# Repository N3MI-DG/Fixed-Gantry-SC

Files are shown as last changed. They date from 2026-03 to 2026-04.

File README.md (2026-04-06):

# Fixed Gantry StealthChanger Mod

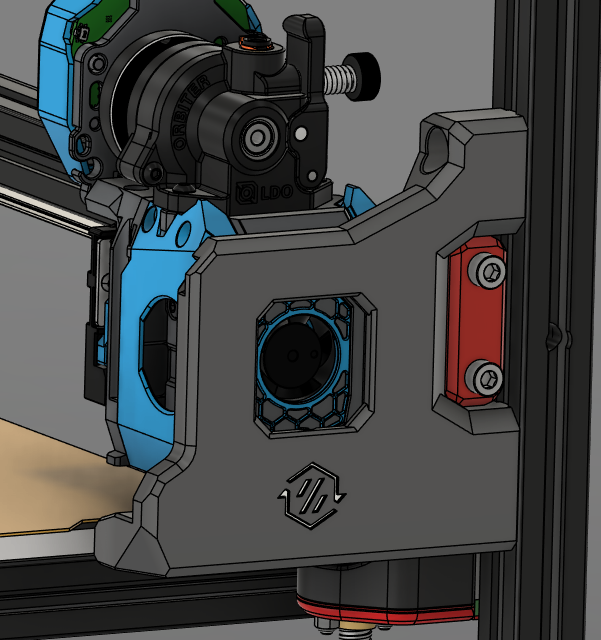
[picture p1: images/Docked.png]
Docked


## Overview

This mod adds StealthChanger capability to fixed gantry printers. It uses a custom dock design that mounts directly to the printer frame and uses a ramping system to mount the toolhead.

The ramping is broken into two actions:

1. The tool runs into the dock in the Y direction, lifting it partially and aligning the screws that are on the tool to the dock.
2. The tool then gets shoved in the X direction to fully lift the tool from the shuttle and engage with the dock.

While a little crude, it works really well and is very reliable.

## Printing

Print with Typical Voron Recommended settings

* `Layer Height` - 0.2mm
* `Extrusion Width` - 0.4mm, forced
* `Infill Percentage` - 40%
* `Infill Type` - Grid, Gyroid, honeycomb, Triangle or Cubic
* `Wall Count` - 4
* `Solid Top/Bottom Layers` - 5
* `Layer Height` - 0.2mm
* `Supports` - Not required, models have built in supports.

## Credits

[DraftShift Design](https://github.com/DraftShift) - StealthChanger

[hartk1213](https://github.com/hartk1213) - Anthead and Umbilical plate aesthetics.

[Armchair-Heavy-Industries](https://github.com/Armchair-Heavy-Industries) - A4T

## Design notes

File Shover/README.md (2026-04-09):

# Shover for Fixed Gantry StealthChanger

## Printing

Print the shover version for the variant of CNC shuttle you have using typical Voron settings.

## BOM

- M3x6 BHCS x2
- M3x8 BHCS x2
- M3x12 BHCS x2
- M3x16 SHCS x1
- M3 Heat Insert x2
- 4mm OD PTFE 12mm Long x2 (optional)

## Instructions

### Step 1

Remove the built-in supports from the shover.

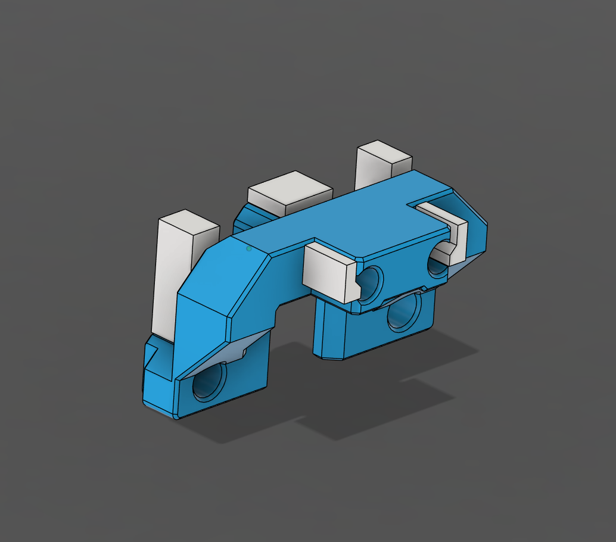
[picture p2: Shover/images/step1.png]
step1


### Step 2

Install 2 M3 heat inserts into the front of the shover.

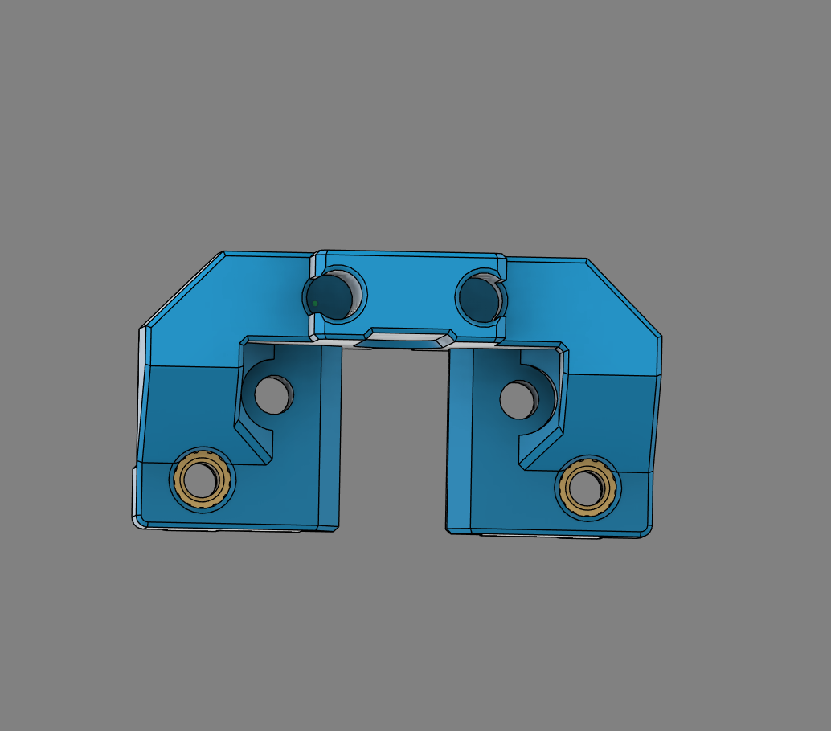
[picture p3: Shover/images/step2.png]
step2


### Step 3

Install a M3x16 SHCS screw into the rear of the shover.

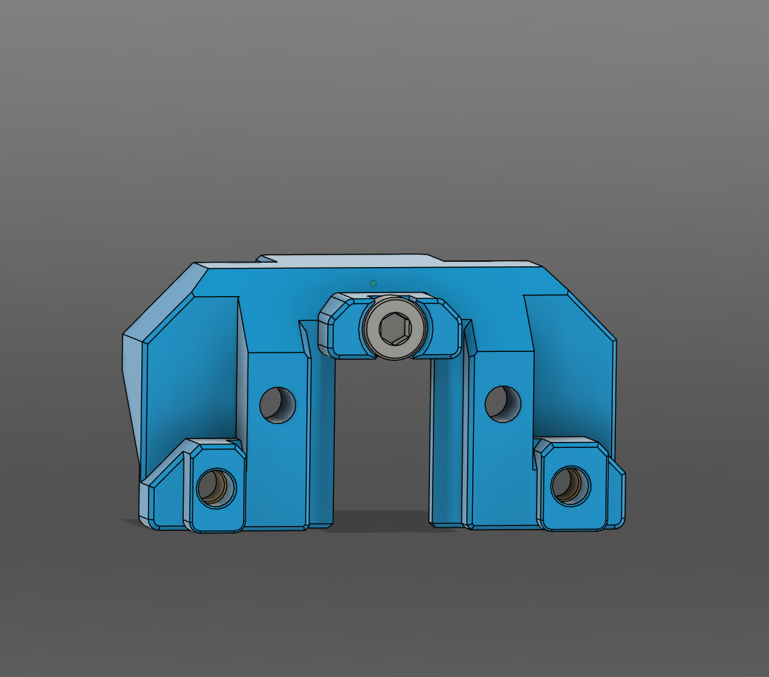
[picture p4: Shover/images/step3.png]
step3


### Step 4

Optionally install 2 12mm pieces of PTFE tube into the front of the shover and trim the corners to match the profile.

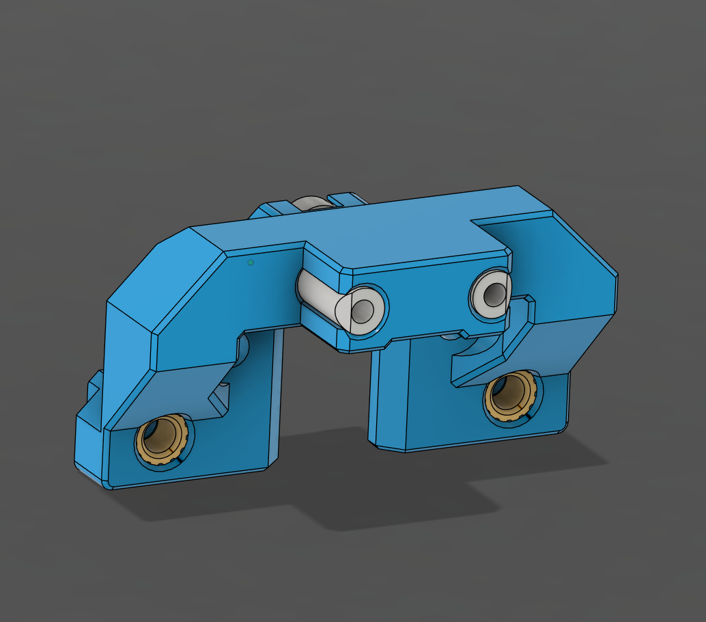
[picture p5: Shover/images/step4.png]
step4


### Step 5

Remove the lower 2 mounting screws from the CNC shuttle and place the shover onto the shuttle. Replace the 2 removed screws with 2 M3x12 BHCS screws.

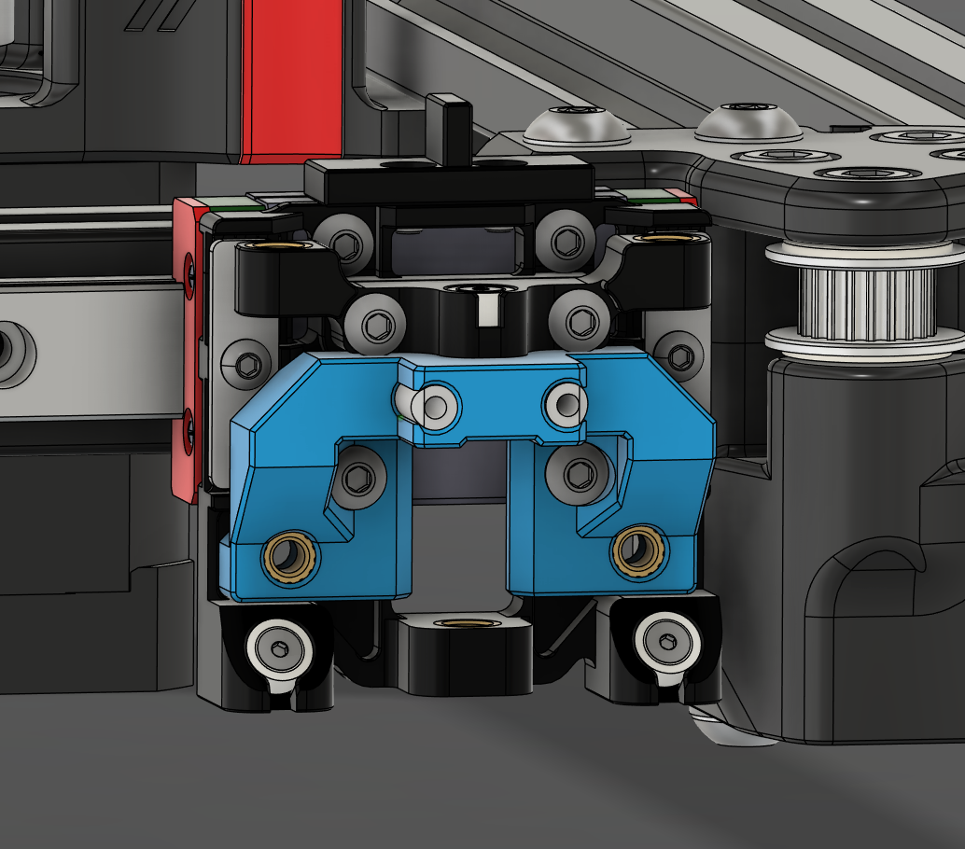
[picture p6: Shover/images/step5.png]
step5


### Step 6

Secure the shover to the CNC shuttle using 2 M3x8 BHCS screws with washers through the heat inserts.

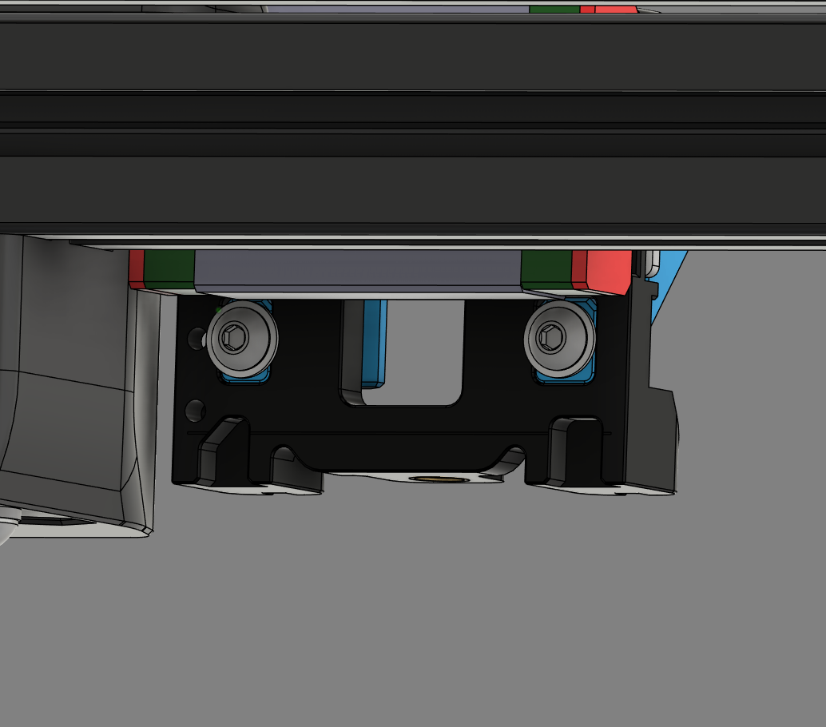
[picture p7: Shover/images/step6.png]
step6


## Testing

After installation, chack that the shover fits neatly in to the backplate of the tool. There should not be any friction between the tool and Shover. If it is too loose without the PTFE, try adding some. If it is too tight with the PTFE, try shaving the PTFE slightly.

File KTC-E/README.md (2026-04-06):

# Klipper-Toolchanger-Easy

To get fixed gantry working on klipper-toolchanger-easy, we need a custom pickup and dropoff path per `tool config` and custom pickup and dropoff gcode in the `[toolchanger]` section.

## Example Tool Sections
The pickup and dropoff paths for the tools need to mirrored. To do that we add a custom path to the `tool config`.

### T0

```
[tool T0]
tool_number: 0
extruder: extruder
fan: T0_part_fan
detection_pin: !nhk0:gpio10
params_park_x: 1.7
params_park_y: 0.8
params_park_z: 1
gcode_x_offset: 0
gcode_y_offset: 0
gcode_z_offset: 0.08
params_dropoff_path: [{'x':22, 'y':16}, {'x':22, 'y':0}, {'x':0, 'y':0}]
params_pickup_path: [{'x':0, 'y':0}, {'x':22, 'y':0}, {'x':22, 'y':16, 'verify':1}]
```

### T1

```
[tool T1]
tool_number: 1
extruder: extruder1
fan: T1_part_fan
detection_pin: !nhk1:gpio10
params_park_x: 302.7
params_park_y: 1.0
params_park_z: 0
gcode_x_offset: -0.290
gcode_y_offset: -1.240
gcode_z_offset: -0.60
params_dropoff_path: [{'x':-22, 'y':16}, {'x':-22, 'y':0}, {'x':0, 'y':0]
params_pickup_path: [{'x':0, 'y':0}, {'x':-22, 'y':0}, {'x':-22, 'y':16, 'verify':1}]
```

## Toolchanger Section
To add custom pickup and dropoff gcodes to the `[toolchanger]` section, add the following to the bottom of the `[toolchanger]` section. This will override the original pickup and dropoff gcodes which are intended for a Voron 2.4.

```
dropoff_gcode:
  {% set x = tool.params_park_x|float %}
  {% set y = tool.params_park_y|float %}
  {% set z = tool.params_park_z|float %}
  {% set fast = tool.params_fast_speed|float %}
  {% set path = tool.params_dropoff_path %}
  {% set max_z = printer.configfile.config["stepper_z"]["position_max"]|float %}
  {% set cur_z = printer.toolhead.position[2]|float %}
  RESPOND TYPE=echo MSG='Dropping off {tool.name}'
  G90
  ; Move 1 mm up to avoid crashing into things
  G0 Z{ [cur_z+1.0, max_z]|min } F{fast}
  #   ##############  Move up to the dock  ##############
  ROUNDED_G0 X={x + path[0]['x']|float} D=150 F={fast}
  ROUNDED_G0 Y={y + path[0]['y']|float} D=0 F={fast}
  STOP_CRASH_DETECTION
  #  ############## Run the path ##############
  {% for pos in path %}
    {% set speed = tool.params_path_speed|float * (pos.get('f', 1.0)|float) %}
    G0 {% if 'x' in pos %}X{x + pos['x']|float}{% endif %} {% if 'y' in pos %}Y{y + pos['y']|float}{% endif %} {% if 'z' in pos %}Z{z + pos['z']|float }{% endif %} F{speed}
  {% endfor %}
  ## Return to safe Y if no pickup_tool
  {% if pickup_tool is none %}
    G0 Y{tool.params_safe_y} F{fast}
  {% endif %}

pickup_gcode:
  {% set x = tool.params_park_x|float %}
  {% set y = tool.params_park_y|float %}
  {% set z = tool.params_park_z|float %}
  {% set fast = tool.params_fast_speed|float %}
  {% set path = tool.params_pickup_path %}
  RESPOND TYPE=echo MSG='Picking up {tool.name}'
  G90
  #   ##############  Fast to the last point  ##############
  ROUNDED_G0 Y={tool.params_close_y} F={fast} D=5
  # ROUNDED_G0 X={x} Z={z + path[0]['z']|float} F={fast} D=5
  ROUNDED_G0 X={x} F={fast} D=5
  ROUNDED_G0 Y={y + path[0]['y']|float} F={fast} D=0
  # Wait for temp before actually picking up the tool, while the nozzle is resting on it's pad.
  {% if tool.extruder %}
    M109 T{tool.tool_number} S{printer[tool.extruder].target|int}
  {% endif %}
  # Run the path
  {% for pos in path %}
    {% set speed = tool.params_path_speed|float * (pos.get('f', 1.0)|float) %}
    G0 {% if 'x' in pos %}X{x + pos['x']|float}{% endif %} {% if 'y' in pos %}Y{y + pos['y']|float}{% endif %} {% if 'z' in pos %}Z{z + pos['z']|float }{% endif %} F{speed}
    {% if 'verify' in pos %}
      VERIFY_TOOL_DETECTED T={tool.tool_number}
    {% endif %}
  {% endfor %}
  # Restore the position with smooth rounded move.
  ROUNDED_G0 Y={tool.params_safe_y} F={fast} D=20
  ROUNDED_G0 D=0
```

## Z Tilt

The Z tilt positions will need to be adjusted because of the tool's docked position. This is an example of what I am using on my 300 Trident.

```
[z_tilt]
z_positions:
  -50, 18
  150, 348
  350, 18
points:
  20, 25
  152.5, 250
  285, 25
```

### Macro to remove tool during Z tilt (Cartographer Only)

```
[gcode_macro Z_TILT_ADJUST]
rename_existing: ZZ_TILT_ADJUST
gcode:
  {% if printer.toolchanger.tool_number != -1 %}
    UNSELECT_TOOL
  {% endif %}

  ZZ_TILT_ADJUST
  ```

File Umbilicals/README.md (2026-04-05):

# Umbilicals for Fixed Gantry StealthChanger (Trident)

## Printing

### TPU

- Clip x2 Minimum (More clips or cable ties can be used to hold the cable and PTFE together over the length of the umbilical.)
- Terminator x1
- Terminator (Mirrored) x1

### ABS/ASA

- Face Plate x1
- Outer Plate x1
- Cover Left x1
- Cover Right x1
- LED Diffuser x1 (Optional)

## BOM

- M3x6 BHCS x2
- M3x10 SHCS x4
- M5x10 BHCS x2
- M3 Heat Insert x8
- M5 Roll-in T Nut x2
- 3x0.3mm Flat Spring Steel x2

## Instructions

### Step 1

Install 6 M3 heat inserts in to the Face Plate.

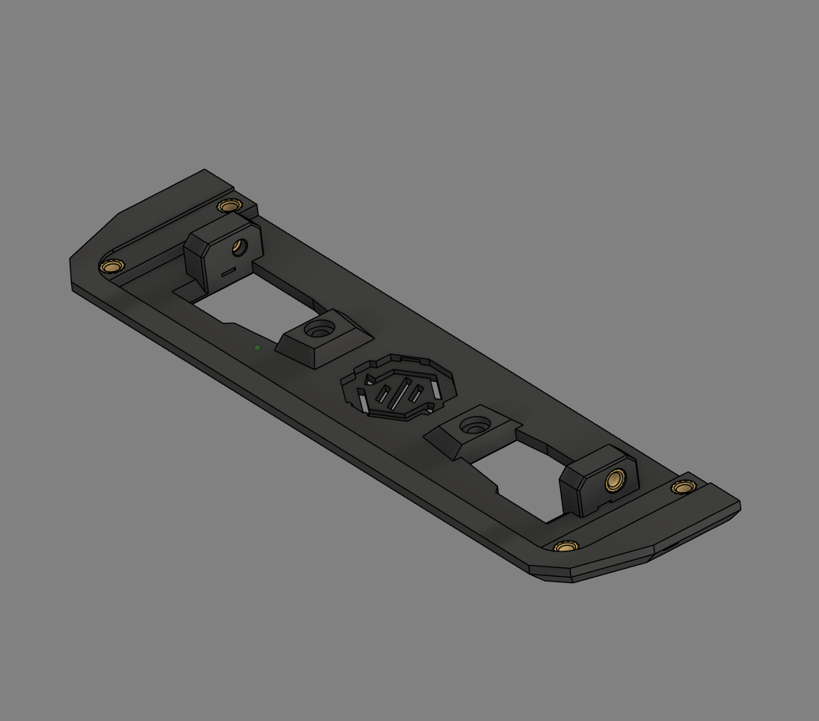
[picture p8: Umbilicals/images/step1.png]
step1


### Step 2

Install a heat insert in to each of the covers.

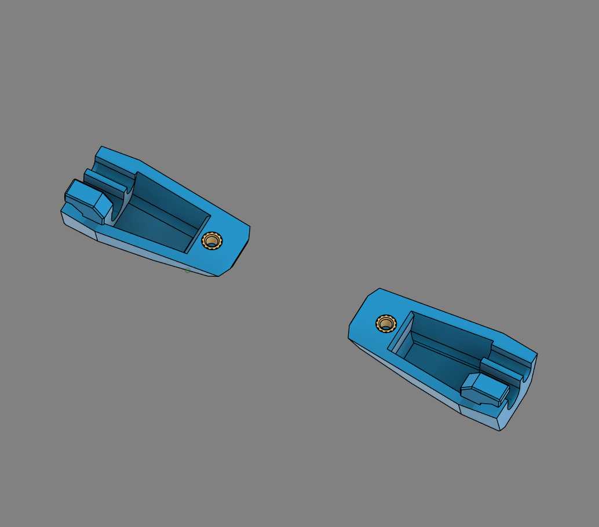
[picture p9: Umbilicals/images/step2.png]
step2


### Step 3 (Optional)

Install the diffuser in to the Face Plate.

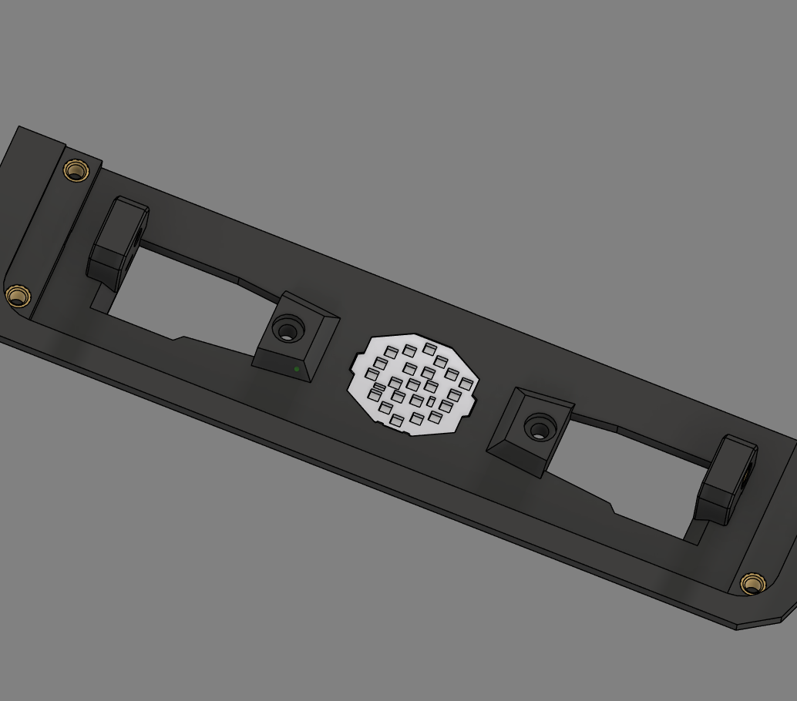
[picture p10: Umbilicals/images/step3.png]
step3


### Step 4 (Optional)

Apply 1mm foam around the perimiter of the Face Plate.

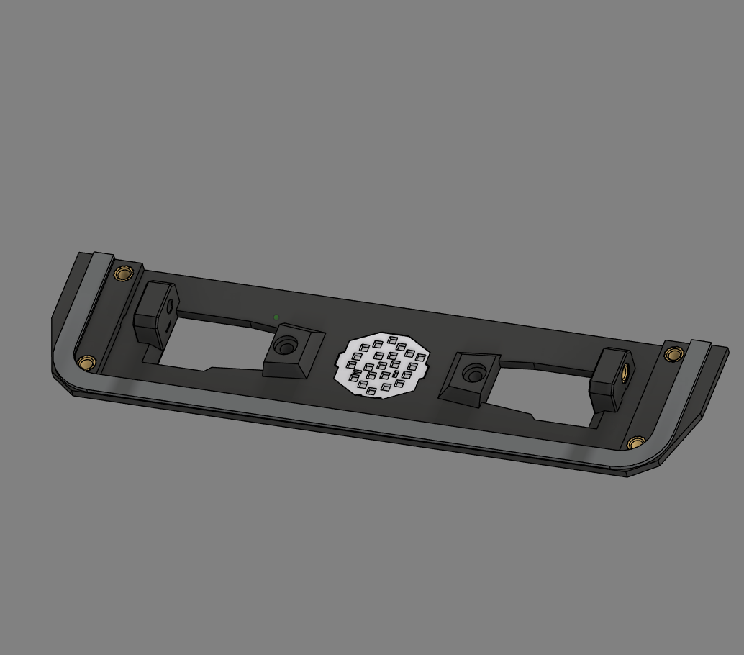
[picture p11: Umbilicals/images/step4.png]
step4


### Step 5

Bend a piece of 3x0.3mm spring steel 90 degrees and feed it through the faceplate. To get the correct length, the spring steel should reach the inside of the printers frame when the faceplate is in place.

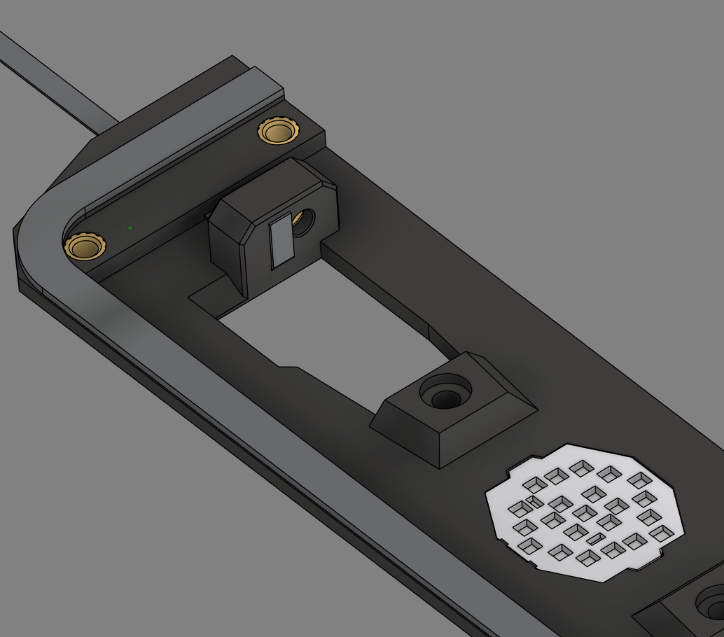
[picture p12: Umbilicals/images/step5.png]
step5


### Step 6

Secure both pieces of spring steel with a m3x6mm BHCS screw.

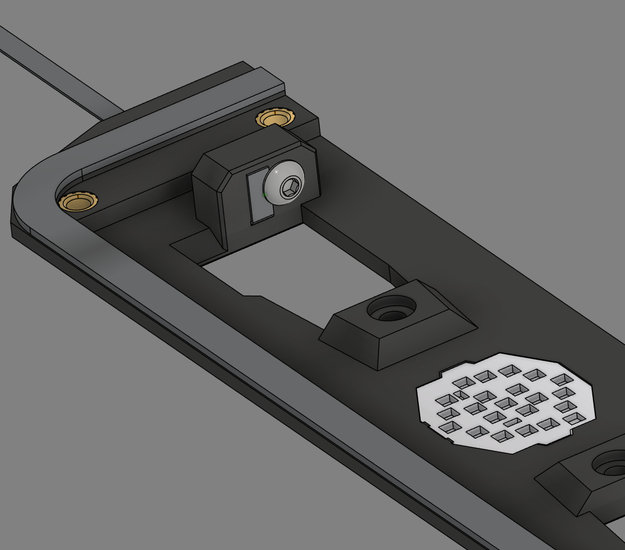
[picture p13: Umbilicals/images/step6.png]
step6


### Step 7

Install a TPU Clip and Terminatior ensuring the orientation is correct. The cable should be on the bottom and PTFE on top.

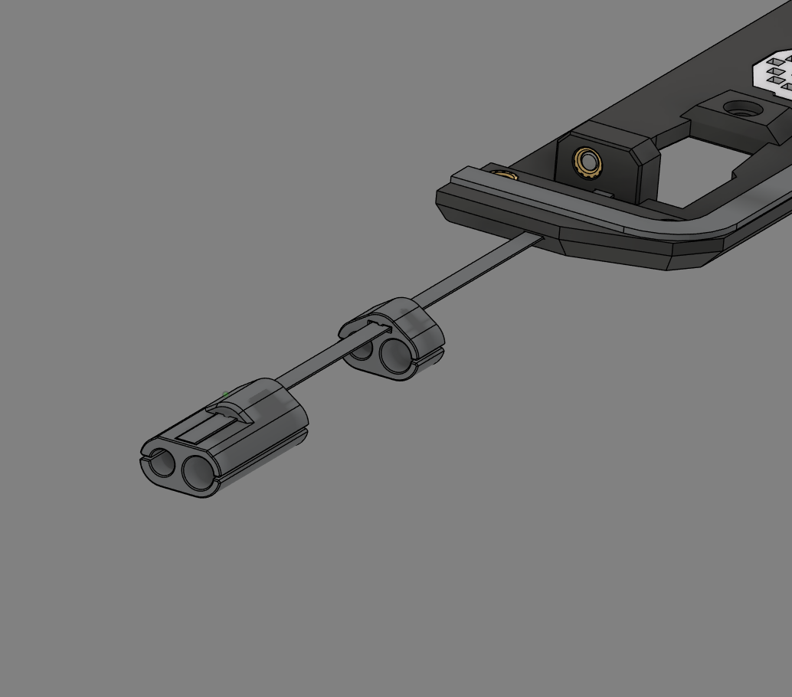
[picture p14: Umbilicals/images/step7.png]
step7


### Step 8

Put a small bend in the end of the spring steel to keep the TPU Terminator in place.

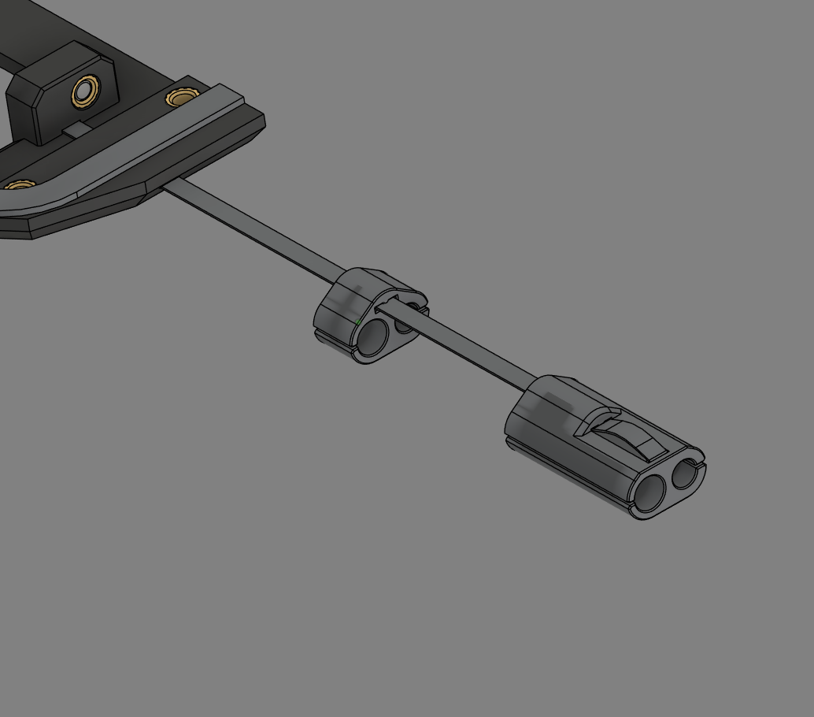
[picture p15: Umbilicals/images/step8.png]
step8


### Step 9

Attach the Outer Plate to the printer using 2 M5x10 BHCS screws and 2 M5 roll-in T nuts.

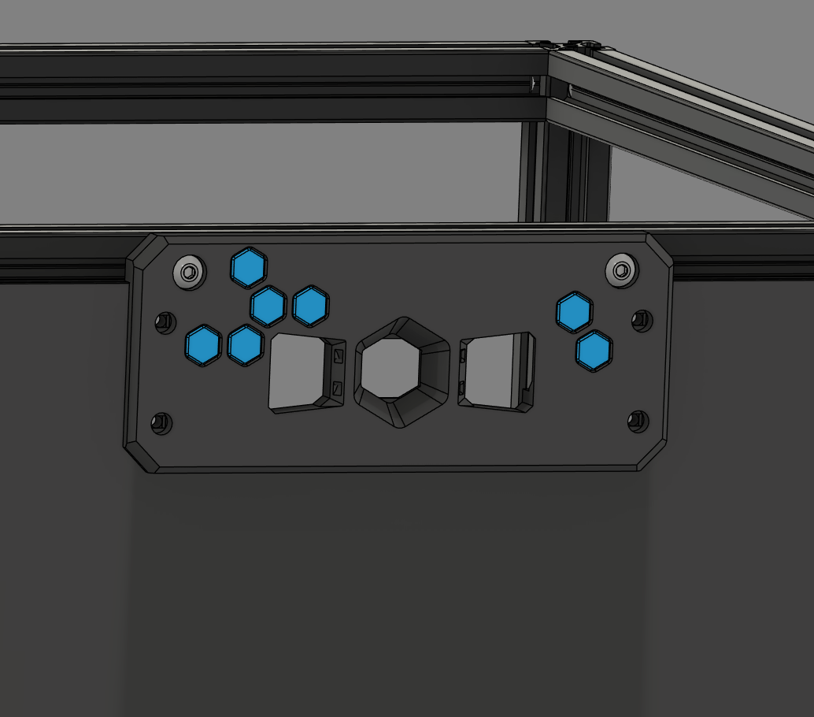
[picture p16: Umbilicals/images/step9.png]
step9


### Step 10 ( Optional)

Install a SC Barf LED.

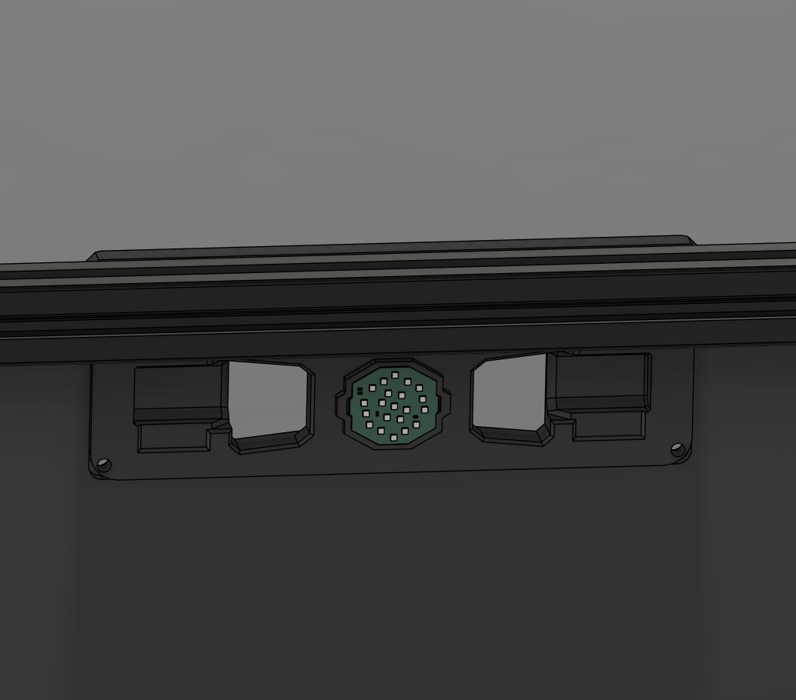
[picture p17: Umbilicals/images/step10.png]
step10


### Step 11

Attach the Face Plate to the Outer Plate using 4 M3x10 BHCS screws.

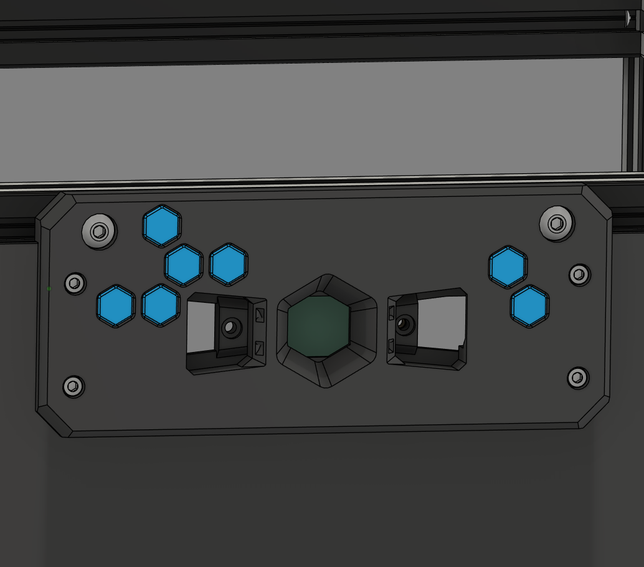
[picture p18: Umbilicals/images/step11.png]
step11


### Step 12

Feed the cables and PTFE tubes through and attach them to the toolheads. Once an umbilical length is determined place the cables and PTFE tubes in to their respective TPU Clip and Terminatior.

### Step 13

Slot the Covers in place and secure with a M3x8 BHCS screw.

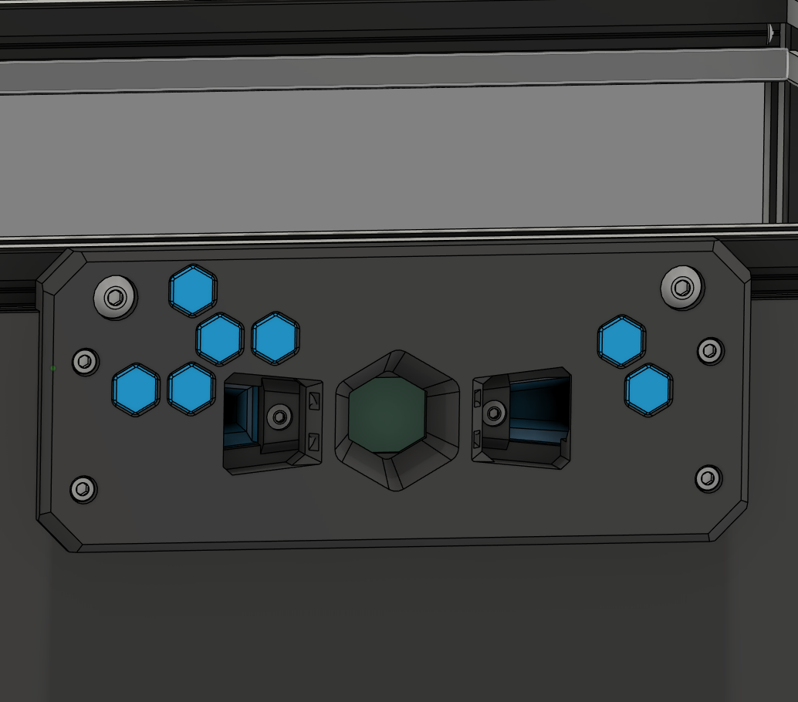
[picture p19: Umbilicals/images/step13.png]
step13


### Step 14

Secure umbilical at the rear of the printer with a ziptie.

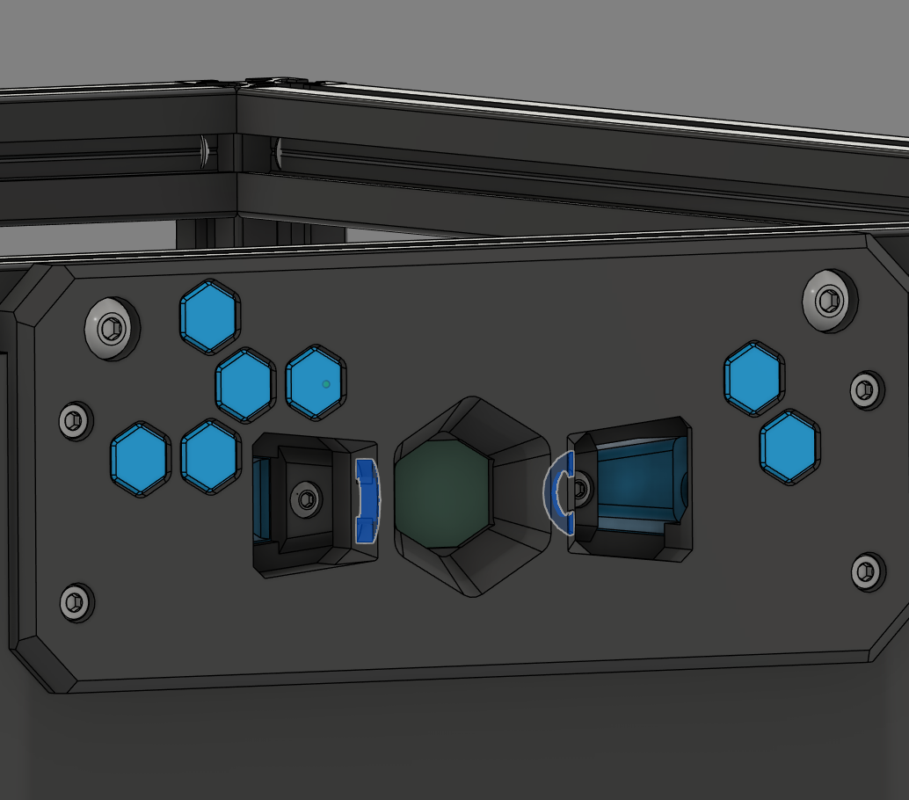
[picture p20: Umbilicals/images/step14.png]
step14


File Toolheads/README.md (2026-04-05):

# Toolheads for Fixed Gantry StealthChanger

The Anthead and A4T are currently supported. Others may be added in the future.

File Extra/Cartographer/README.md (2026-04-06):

# Cartographer Mount

## Printing

- CNC Cartographer Mount x1
- CNC Cartographer Arm x1

## BOM

- M3x20 SHCS x1
- M3x16 SHCS x1
- M3x12 SHCS x1
- M3 Heat Insert x3

## Instructions

### Step 1

Remove built-in supports from the Cartographer Mount.

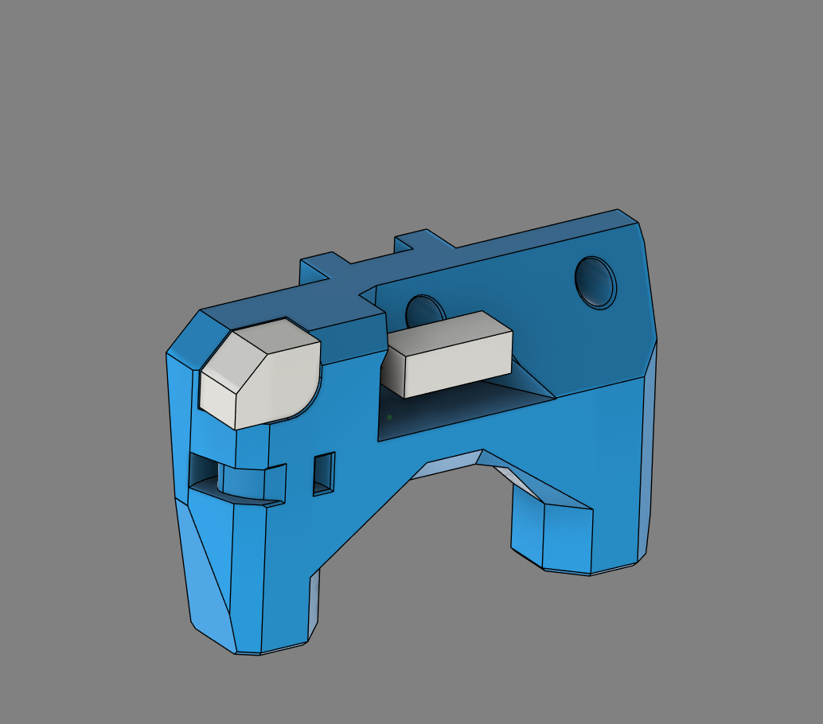
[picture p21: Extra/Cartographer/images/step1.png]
step1


### Step 2

Install 2 heat inserts in to the bottom of the Cartographer Mount.

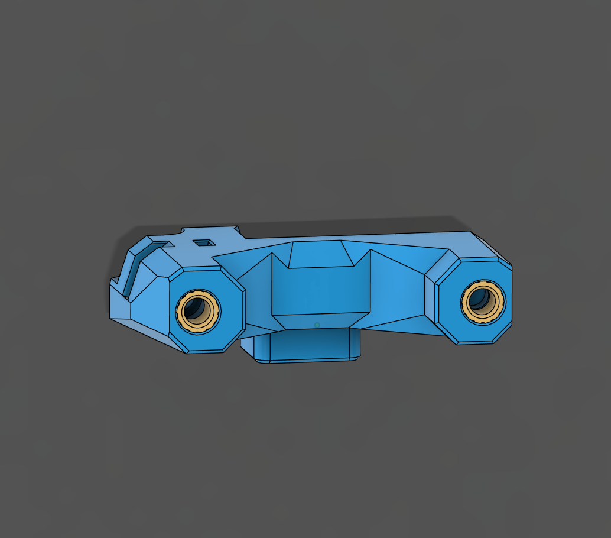
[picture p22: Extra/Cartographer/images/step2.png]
step2


### Step 3

Install a heat insert in to the Cartographer Arm.

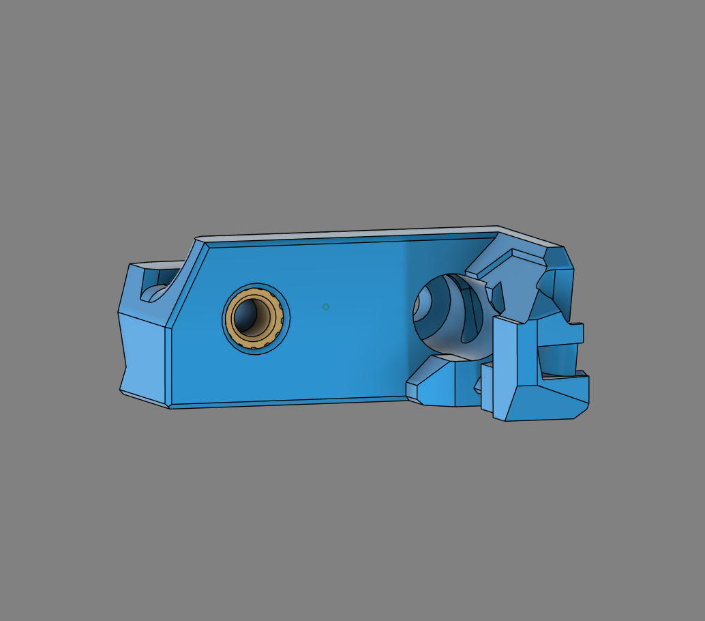
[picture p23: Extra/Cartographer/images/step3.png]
step3


### Step 4

Attach the Cartographer Arm to the Mount with a M3x20 SHCS screw.

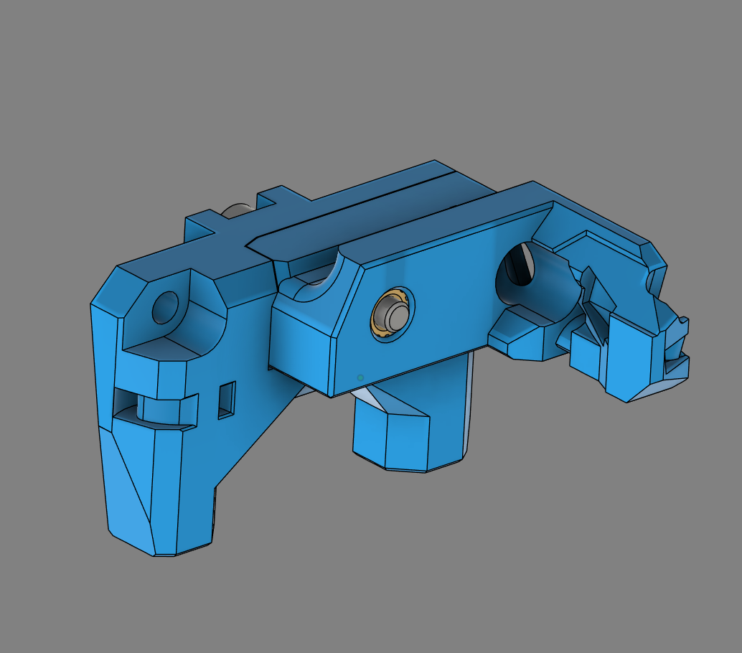
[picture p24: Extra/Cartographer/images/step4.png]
step4


### Step 5

Attach the Cartographer to the mount using the supplied flat screws.

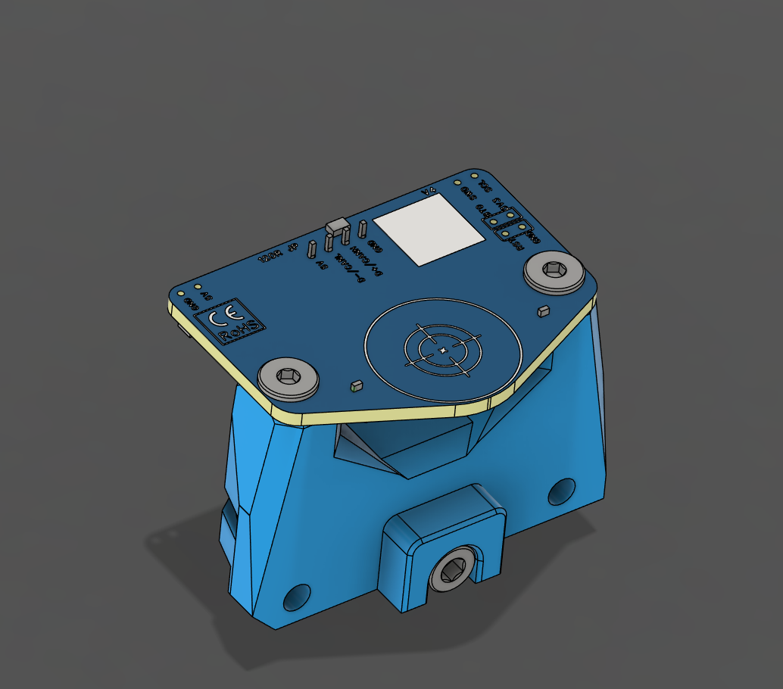
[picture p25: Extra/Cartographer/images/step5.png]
step5


### Step 6

Route the cable through the provided channels and secure using 3 cable ties.

step6

### Step 7

Attach the Cartographer Mount to the Shover On the CNC Shuttle using a M3x12 SHCS screw and a M3x16 SHCS screw.

step7

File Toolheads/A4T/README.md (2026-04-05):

# A4T

All of the A4T cowl variants have been provided, but depending on the cowl variant, some may not be suitable.

The Dragon/Rapido UHF variant in particular has the hotend fan significantly blocked by the dock.

## Printing

- Cowl for your specific hotend.
- Low Rider StealthChanger backplate.

## BOM (Per Toolhead)

- M3x12 BHCS x2

## Instructions

The A4T for this mod requires a custom Cowl and StealthChanger Backplate. The complete toolhead will need to be built.

### Step 1

Assemble the A4T As you would typically, substituting the Cowl and StealthChanger Backplate for the version from this repository.

step1

### Step 2

Install 2 M3x12 BHCS screws in to the front of the cowl. Screw them in until the screw head is ~3mm away from the front of the duct. These will need to be tuned later.

step2

### Step 3

Install a 6x3mm magnet in the bottom of either the left or right side of the StealthChanger Backplate. These magnets can be held in place with either glue or an M2x8 FHCS screw and are only required for the side of the printer the tool will rest in.

NOTE: The magnet needs to attract to the top magnet in the dock's blocker. Make sure it is orientated correctly. 

step3

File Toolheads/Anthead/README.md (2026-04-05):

# Anthead

SF version only.

## Printing

- Left duct
- Right duct

## BOM (Per Toolhead)

- M3x12 BHCS x2

## Instructions

The Anthead for this mod is much the same as the Anthead for a typical StealthChanger. The only difference being modified ducts.

### Step 1

Replace the stock Fan Ducts with the version supplied in this repository.

step1

### Step 2

Install an M3x12 BHCS screw to each of the Fan Ducts. Screw them in until the screw head is ~3mm away from the front of the duct. These will need to be tuned later.

step2

### Step 3

Install a 6x3mm magnet in the bottom of either the left or right side of the duct. These magnets should be held in place with glue and are only required for the side of the printer the tool will rest in.

NOTE: The magnet needs to attract to the top magnet in the dock's blocker. Make sure it is orientated correctly. 

step3

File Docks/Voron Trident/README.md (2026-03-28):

# Voron Trident Docks for StealthChanger

## Printing
For each dock, you will need to print:

- Dock body for your idler configuration.
- Blocker for the chosen toolhead.
- LED diffuser.

## BOM (Per Dock)

All required hardware for the docks can be obtained from the LDO tool and dock kit. 
There are provisions for countersunk 6x3 magnets for the blockers and docks if you have them available.

- M3x6 BHCS x3
- M3x40 SHCS x1
- M5x10 BHCS x2
- M5 Roll-in T Nut x2
- M3 Heat Insert x2
- StealthChanger Wiper x1
- 6x3 Magnet (N52) x4
- 5x2 Magnet (N52) x2
- SC Barf LED x1 (optional)
- M3x6 BHCS x1 (optional)

## Instructions

### Step 1

Install 2 M3 heat inserts in to the bottom of the Blocker.

step1

### Step 2

Install a 6x3mm magnet in to the bottom of the blocker. Use either glue or a M2x8 FHCS screw to secure it depending on the magnet type.

step2

### Step 3

Install a 6x3mm magnet in to the top of the blocker. Use either glue or a M2x8 FHCS screw to secure it depending on the magnet type.

NOTE: The top magnet needs to attract to the bottom of the toolhead. Ensure you install the magnet in the correct orientation.

step3

### Step 4

Insert the wiper in to the blocker and secure with 2 M3x6 BHCS screws. These screws can be loosened to adjust the wiper position later.

step4

### Step 5

Install the wiper tension screw in the bottom of the blocker by screwing it in to the plastic. It doesn't need to be tightened, it is used later to adjust the pressure applied to the nozzle.

step5

### Step 6

Install a 6x3mm magnet in to the bottom of the dock. Use either glue or a M2x8 FHCS screw to secure it depending on the magnet type.

NOTE: The magnet needs to attract to the bottom of the blocker. Ensure you install the magnet in the correct orientation.

step6

### Step 7

Install 2 5x2mm magnets in to the screw slots of the dock. Use glue to secure them.

step7

### Step 8

Install the LED diffuser by pushing the bottom in first and then pushing the top in to place. If you are not using an LED, you can add some glue to help keep it in place.

step8

### Step 9 (Optional)

Place the SC Barf LED in place and secure with an M3x6 BHCS screw.

step9

### Step 10

Install the blocker with an M3x40 SHCS screw. Do not over tighten, the blocker needs to be able to rotate freely on the screw.

step10

### Step 11 

Mount the dock on the printer using 2 M5x10 BHCS screws and 2 M5 roll-in T-nuts. The dock fits over the gantry's idler.

step11

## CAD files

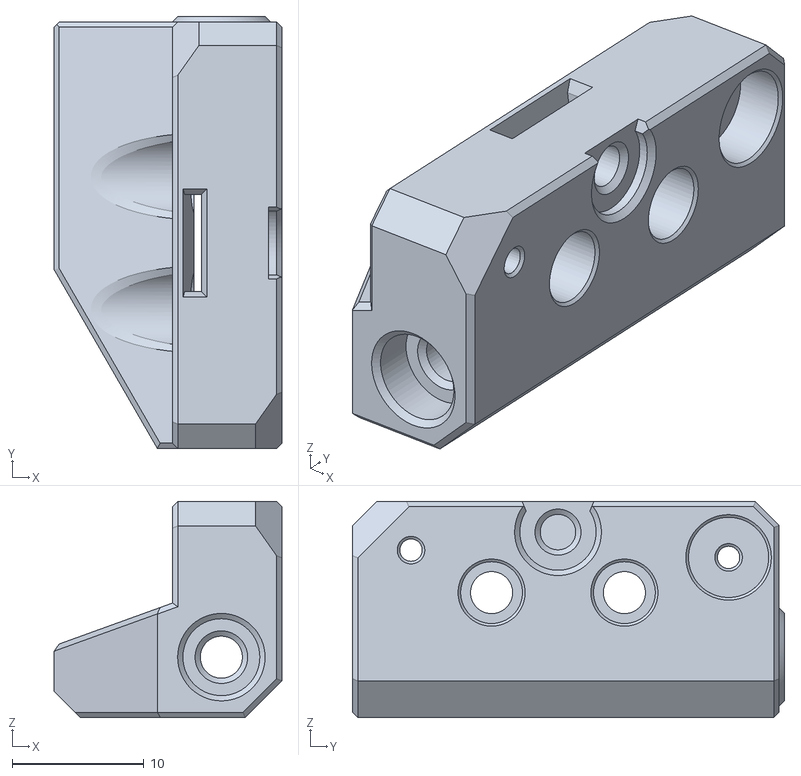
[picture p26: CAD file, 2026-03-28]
Docks/Voron Trident/STLS/Anthead Blocker (Right).stl
17.3 x 32.9 x 16.4

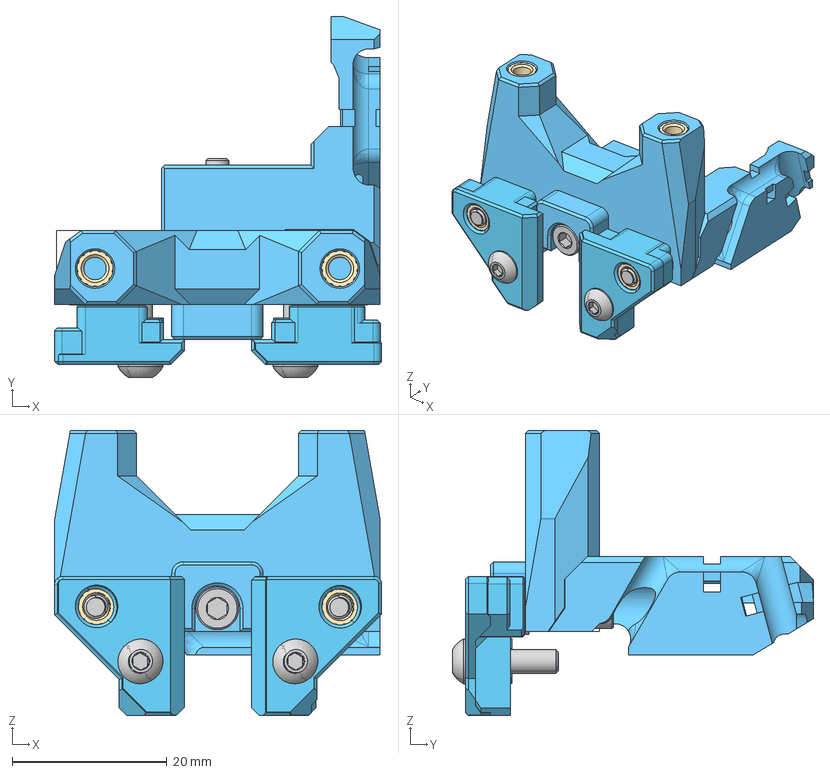
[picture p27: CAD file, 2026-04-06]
Extra/Cartographer/STEP/Carto Mount.step
42.2 x 46.6 x 36.9 mm
CNC Cartographer X Bracket
Supports (8)
M3x12 SHCS
M3x16 SHCS
M3x20 SHCS
(Unsaved) x 3
M3x8 BHCS x 2
(Unsaved)_1 x 2
M3 Shim Washer x 2
M3x12 BHCS x 2
M3x8 BHCS_1 x 2
(Unsaved)_2 x 2
M3 Shim Washer_1 x 2
M3x12 BHCS_1 x 2

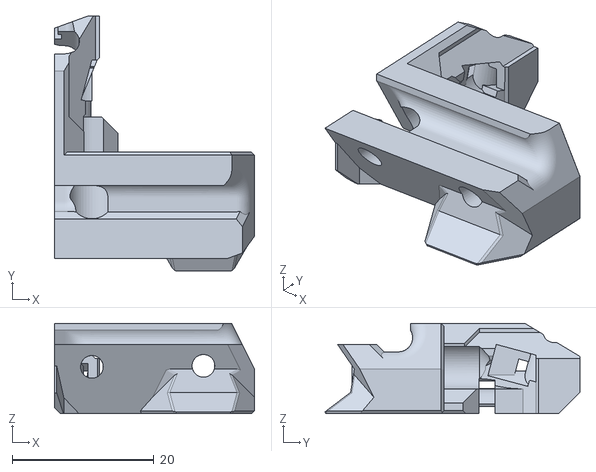
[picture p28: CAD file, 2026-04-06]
Extra/Cartographer/STL/CNC Cartographer Arm.stl
28.2 x 36.0 x 12.7

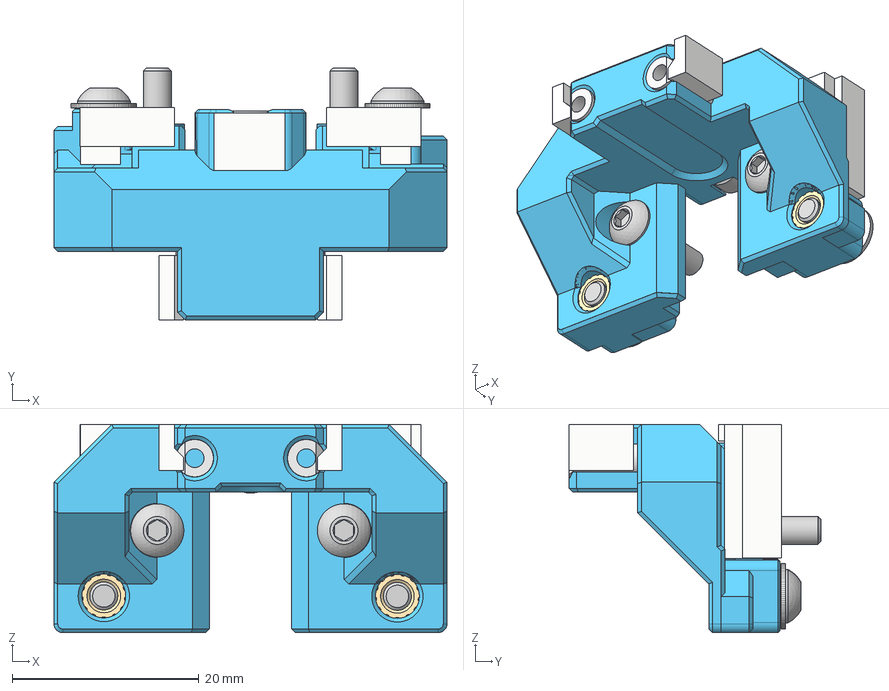
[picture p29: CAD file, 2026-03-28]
Shover/STEP/Shover.step
42.1 x 26.9 x 22.3 mm
M3x8 BHCS x 2
(Unsaved) x 2
M3x16 SHCS
M3 Shim Washer x 2
M3x12 BHCS x 2
PTFE (1)
Supports (7)
M3x8 BHCS_1 x 2
(Unsaved)_1 x 2
M3 Shim Washer_1 x 2
M3x12 BHCS_1 x 2
M3x16 SHCS_1
PTFE
Supports (6)

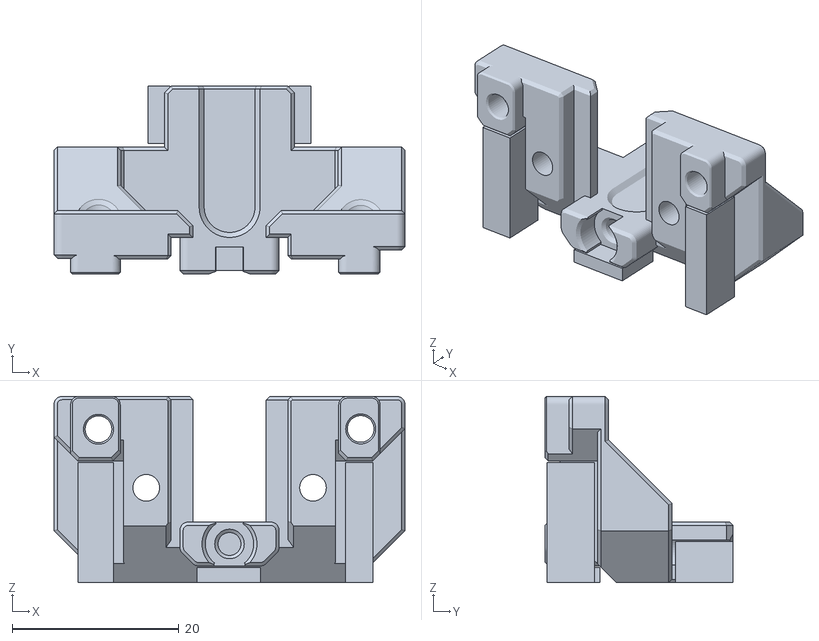
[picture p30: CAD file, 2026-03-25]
Shover/STLS/LDO Shover.stl
42.1 x 22.6 x 22.3

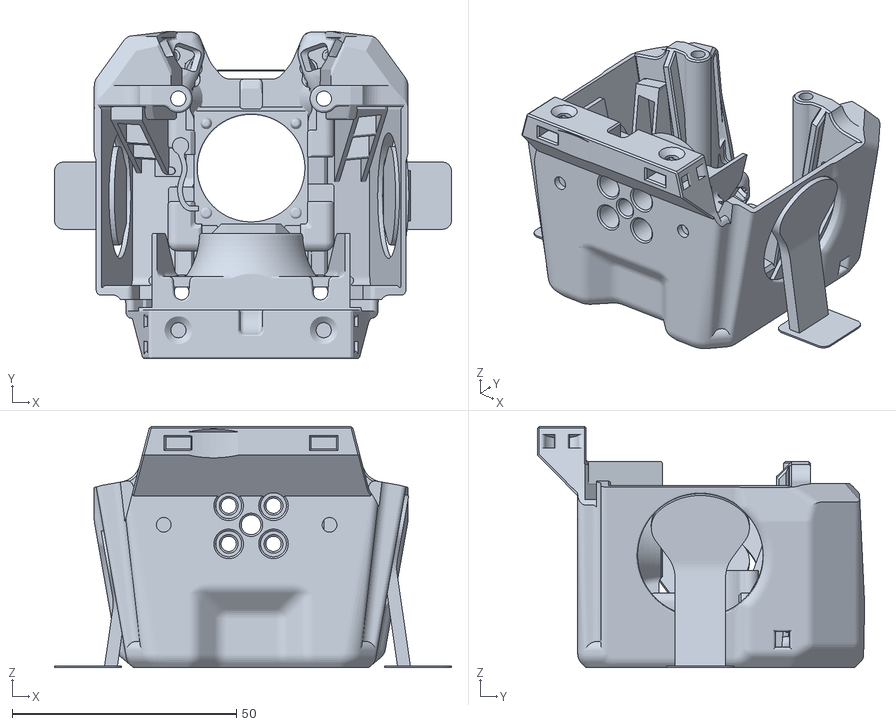
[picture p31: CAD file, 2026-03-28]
Toolheads/A4T/STLS/A4T Cowling - Revo-Voron Orbiter.stl
88.6 x 73.0 x 53.8

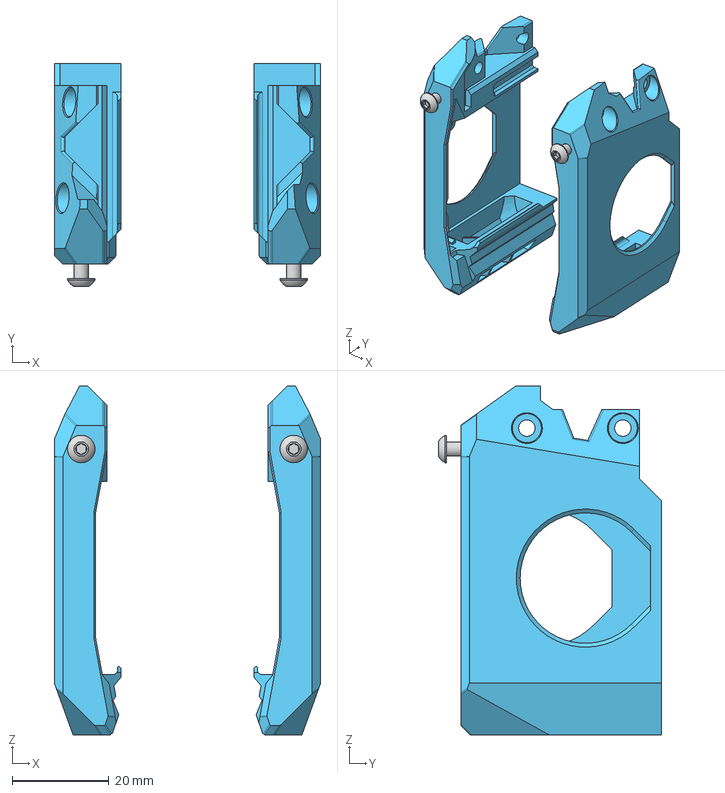
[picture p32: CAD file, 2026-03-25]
Toolheads/Anthead/STEP/Anthead SF Ducts.step
55.2 x 46.3 x 72.3 mm
Right_Duct_Standard
M3x25 BHCS x 2
Left_Duct_Standard

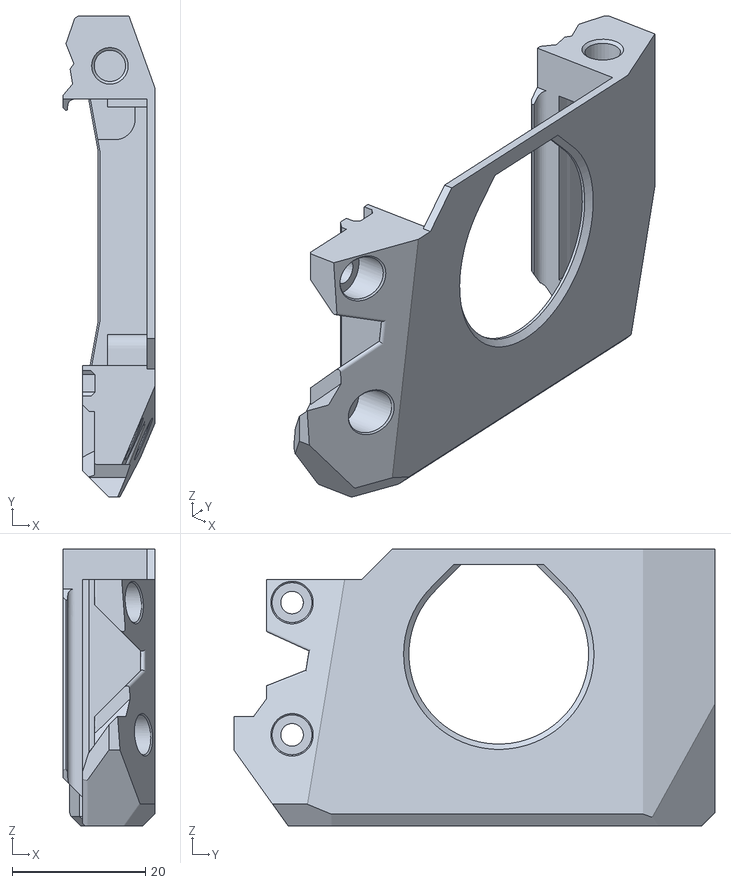
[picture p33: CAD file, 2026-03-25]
Toolheads/Anthead/STLS/Right_Duct_Standard.stl
13.8 x 72.3 x 41.6

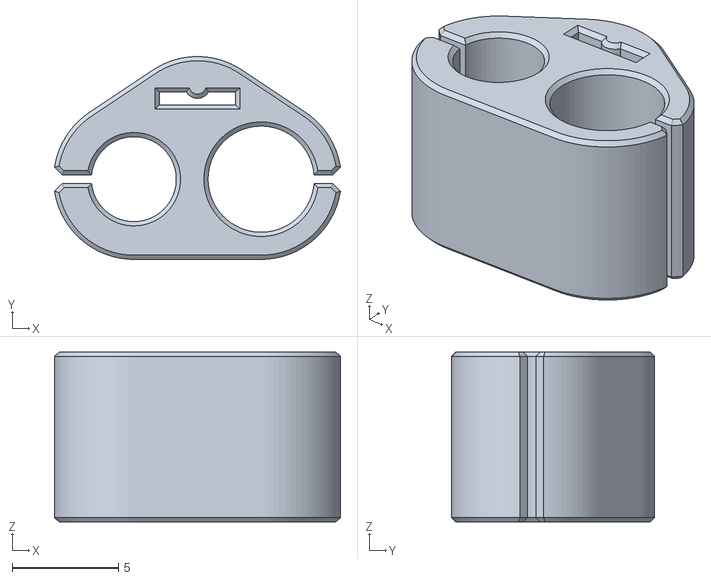
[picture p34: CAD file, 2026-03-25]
Umbilicals/STL/[tpu]_Clip_x2.stl
13.5 x 9.56 x 8.00

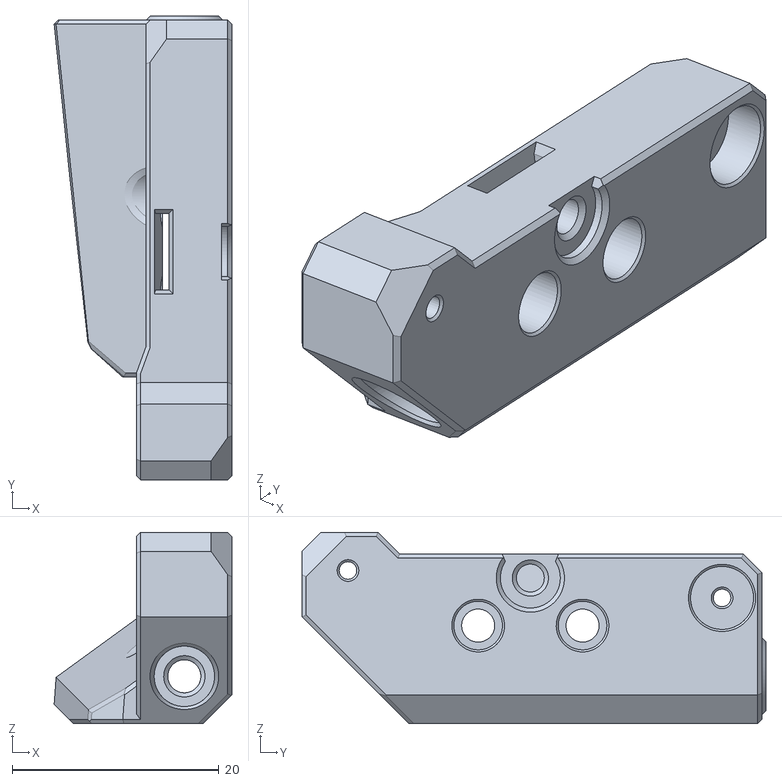
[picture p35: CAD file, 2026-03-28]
Docks/Voron Trident/STLS/A4T Blocker (Right).stl
17.2 x 44.9 x 18.5

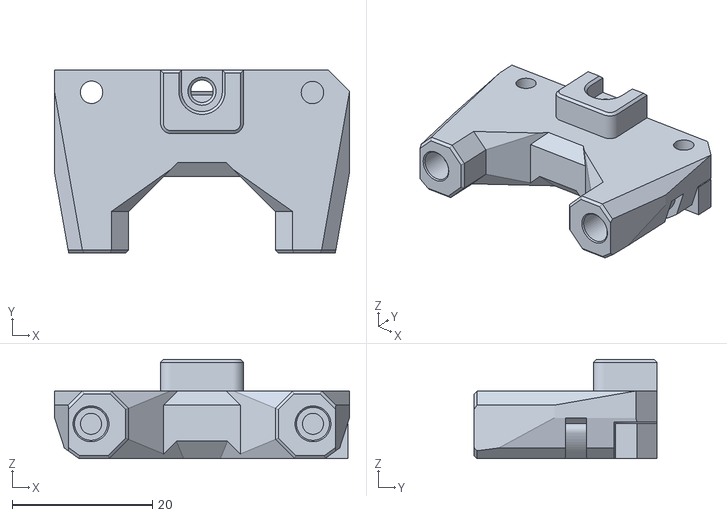
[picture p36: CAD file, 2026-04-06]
Extra/Cartographer/STL/CNC Cartographer Mount.stl
42.0 x 26.0 x 14.1

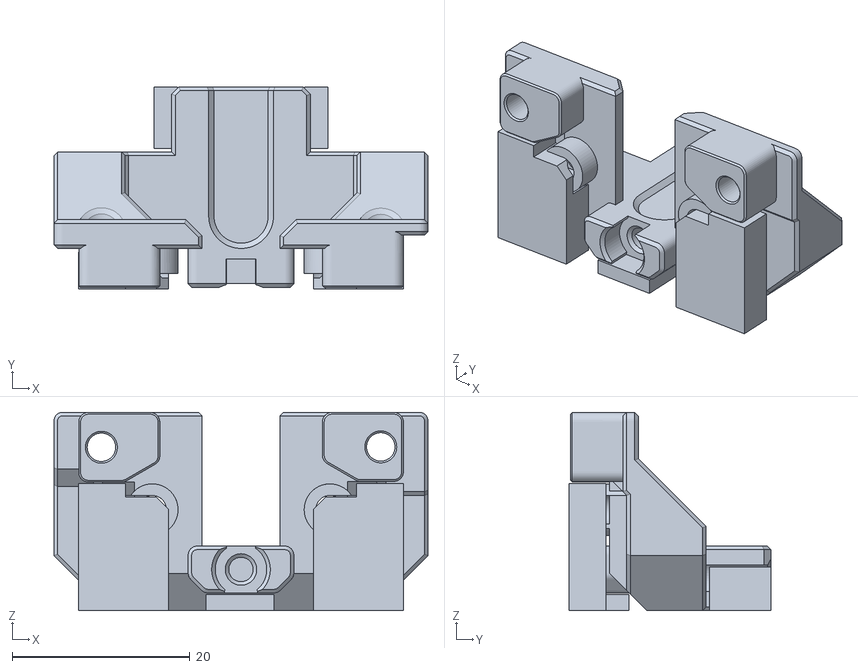
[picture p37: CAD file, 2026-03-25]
Shover/STLS/Fysetc Shover.stl
42.1 x 22.7 x 22.3

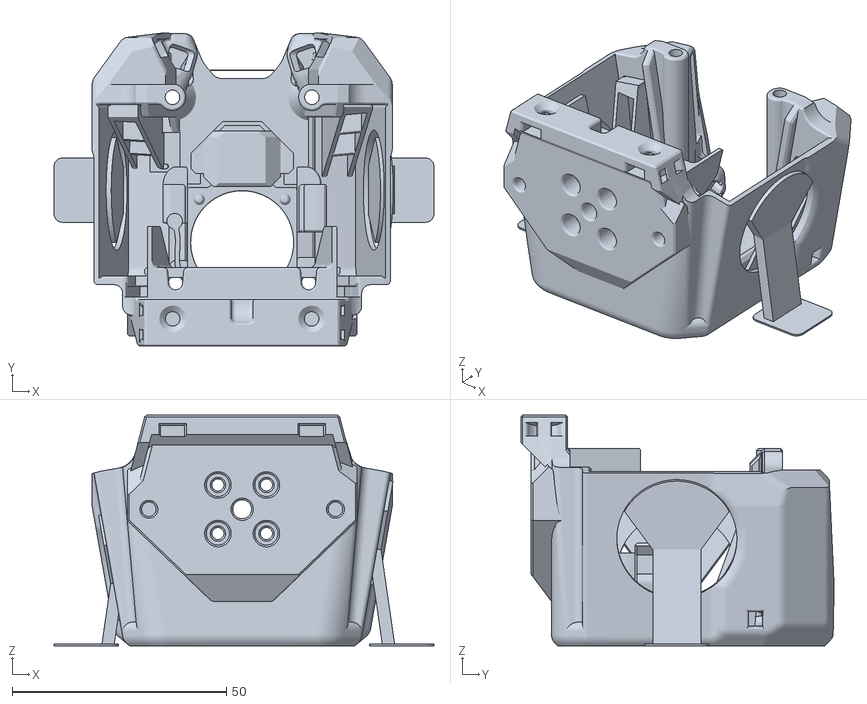
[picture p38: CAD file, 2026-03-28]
Toolheads/A4T/STLS/A4T Cowling - Dragon-Rapido UHF Sherpa.stl
88.6 x 73.0 x 53.8

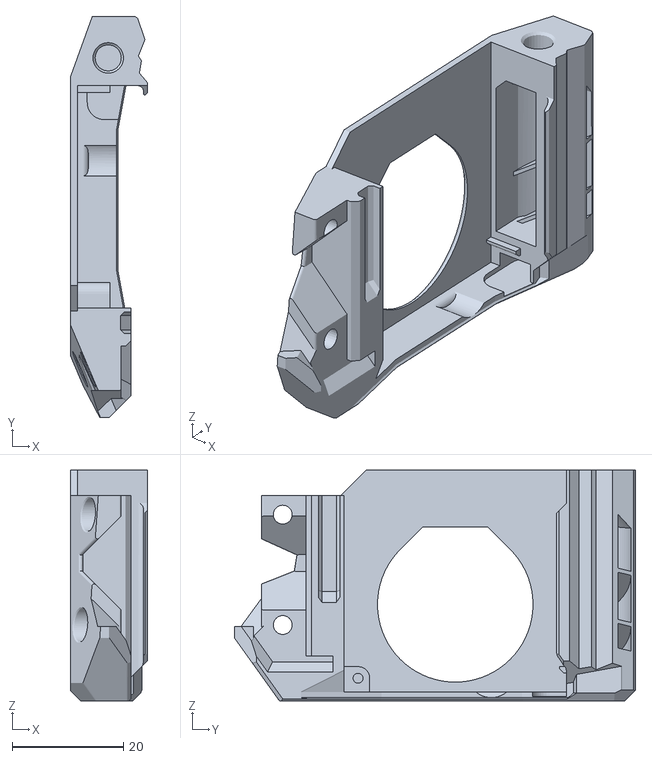
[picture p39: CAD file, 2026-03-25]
Toolheads/Anthead/STLS/Left_Duct_Standard.stl
13.8 x 72.3 x 41.6

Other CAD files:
Umbilicals/STL/Face_Plate.stl
Docks/Voron Trident/STLS/A4T Blocker (Left).stl
Toolheads/A4T/STLS/A4T Cowling - Dragon_Rapido Sherpa.stl
Umbilicals/STL/Face_Plate_SC.stl
Docks/Voron Trident/STLS/Anthead Blocker (Left).stl
Docks/Voron Trident/STLS/SC LED Diffuser.stl
Docks/Voron Trident/STLS/Trident Dock (Left BFI Idler).stl
Docks/Voron Trident/STLS/Trident Dock (Left Stock Idler).stl
Docks/Voron Trident/STLS/Trident Dock (Right BFI Idler).stl
Docks/Voron Trident/STLS/Trident Dock (Right Stock Idler).stl
Toolheads/A4T/STLS/A4T Cowling - Bambulab Orbiter.stl
Toolheads/A4T/STLS/A4T Cowling - Bambulab Sherpa.stl
Toolheads/A4T/STLS/A4T Cowling - Chube Compact Orbiter.stl
Toolheads/A4T/STLS/A4T Cowling - Chube Compact Sherpa.stl
Toolheads/A4T/STLS/A4T Cowling - Dragon-Rapido UHF Orbiter.stl
Toolheads/A4T/STLS/A4T Cowling - Dragon_Rapido Orbiter.stl
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

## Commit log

2026-03-25 Umbilicals, Shover and initial toolheads
    [A4T Cowling - Bambulab Orbiter.stl, A4T Cowling - Bambulab Sherpa.stl, A4T Cowling - Chube Compact Orbiter.stl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]
2026-03-26 Add A4T low rider backplate
    [A4T SC Backplate Low Rider.stl]
2026-03-28 Update A4T Cowls
    [A4T Cowling - Bambulab Orbiter.stl, A4T Cowling - Bambulab Sherpa.stl, A4T Cowling - Chube Compact Orbiter.stl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]
2026-03-28 Add dock files
    [A4T Blocker (Left).stl, A4T Blocker (Right).stl, Anthead Blocker (Left).stl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]
2026-03-28 Add Shover README.md
    [Shover.step]
2026-03-28 Rotate blockers for printing.
    [A4T Blocker (Left).stl, A4T Blocker (Right).stl, Anthead Blocker (Left).stl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]
2026-03-28 Add readme for Trident Docks
    [SC LED Diffuser.stl]
2026-04-05 Add toolhead docs
2026-04-06 Add Cartographer mount
    [CNC Cartographer Arm.stl, CNC Cartographer Mount.stl, Carto Mount.step]
